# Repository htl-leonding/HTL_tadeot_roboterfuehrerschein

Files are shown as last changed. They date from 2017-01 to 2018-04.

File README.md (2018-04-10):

# Roboter Führerschein (Tag der offenen Tür)
Dieses Repository umfasst alle wichtigen Infos sowie den Server und den Client für das Projekt **HOTRoad** (_Himbeerkuchen on the Road_) welches am Tag der offenen Tür unter dem Namen **Roboter Führerschein** vorgeführt wird.

# [DropboxLink](https://www.dropbox.com/sh/1ua68h7xghiqnpn/AAAmZcrnHf75XxftolFobO0Ba?dl=0)

### Was ist alles am Repo?
 - **Client**: Hier befindet sich der Source Code beider Clients, mit denen man den Roboter ansteuren kann. Es gibt einen Desktop-Client für  den Rechner und einen Andriod-Client für das Handy. 
 - **Server**: Hier befindet sich der Source Code für den Server (denn man auf dem Raspberry ausführen muss) welcher die Signale der Clients interpretiert.
 - **FührerscheinBuilder**: Hier befindet sich die Anwendung, mit der man die Führerscheine erstellen und als PDF exportieren kann um diese anschließend auszudrucken.
 - **Requirements**: Hier befindet sich einerseits die mpjpg_streamer Library welche für den Raspberry zum Streamen der Kamerabilder benötigt wird, und die JoyToKey Anwendung welche man benötigt um die Controller Inputs auf die richtigen Tastatur Inputs umwandelt.
 - **Documents**: Hier befinden sich alle wichtigen Information für das Projekt sowie Schaltplan, Liste der Teile etc... .

### Installation Guide
**WARNING**: This guide assumes you have a Raspberry Pi (Model B or newer/better) with Raspbian OS installed and 2 free USB ports. The Raspberry Pi must be connected to the internet and you’ll need to SSH onto it. You should also know how to gain superuser rights, because they are a necessity throughout the guide.

1. **Assembly of the car**<br>
    Use the parts from the given list (_“Stückliste.ods”_) and assemble them as followed:<br>
    ## Circuit Diagram:    
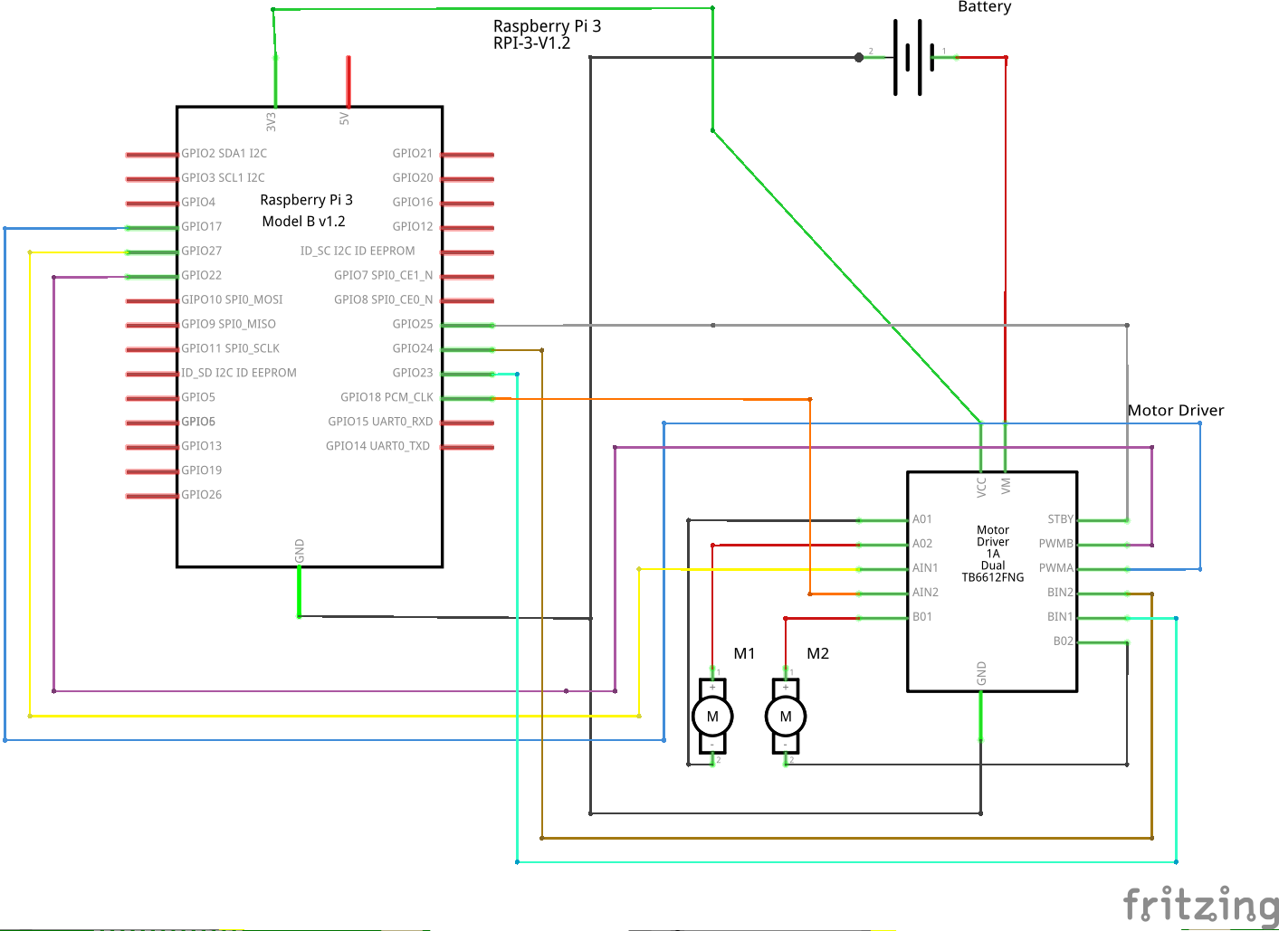
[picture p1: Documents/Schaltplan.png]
Schaltplan
     <br>
    
    ## Fritzing:
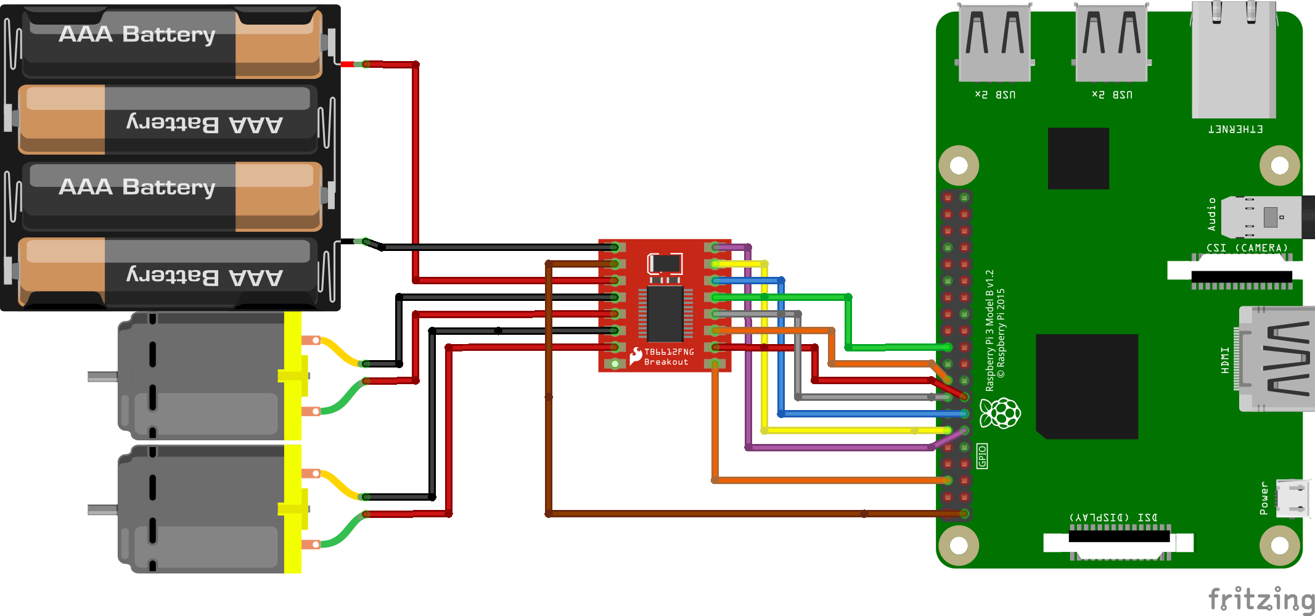
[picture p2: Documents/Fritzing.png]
Fritzing
    
    
2. **Packages, packages, packages**<br>
    You now need to install a few packages, which are necessary for **HOTRoad** to even function. You’ll need:   
    
    ```
    $ apt-get install hostapd isc-dhcp-server libjpeg8-dev imagemagick libv4l-dev
    ```
    Now comes the fun part.

3. **Configuring hostapd**<br>
    Open up “/etc/hostapd/hostapd.conf” add the following lines:
    ```
    interface=wlan0
    driver=nl80211  ---> Use rtl871xdrv for EDIMAX adapters
    ssid=HOTRoad
    hw_mode=g
    channel=11
    wpa=1 wpa_passphrase=himbeerkuchen
    wpa_key_mgmt=WPA-PSK
    wpa_pairwise=TKIP CCMP
    wpa_ptk_rekey=600
    macaddr_acl=0
    ```

    If you know how, change the settings appealing to your needs!
    Now open up **“/etc/default/hostapd”** and add:
	```
	DAEMON_CONF=”/etc/hostapd/hostapd.conf”
    ```
    
    **For EDIMAX adapters**<br>
    If you are using a EDIMAX adapter you need to change the hostapd binary. Copy the given hostapd binary with the following script:
	```
	 $ mv /usr/sbin/hostapd /usr/sbin/hostapd.bak
	 $ cp /home/pi/dat/hostapd /usr/sbin/
	```
	
4. **Configuring isc-dhcp-server**<br>
    Edit **“/etc/dhcp/dhcpd.conf”** and add the following:
	```
	subnet 10.10.0.0 netmask 255.255.0.0 {
        range 10.10.0.25 10.10.0.50;
        option domain-name-servers 8.8.4.4;
        option routers 10.10.0.1;
        interface wlan0;
    }
    ```

    Override the existing settings in **“/etc/network/interfaces”** with:
	```
	iface wlan0 inet static
	address 10.10.0.1
	netmask 255.255.255.0
	```

5. **Configuring mjpg-streamer**<br>
    You need to build the given version of mjpg-streamer (no really, only the given version is working – at least for me). To achieve this you need to follow these commands:
    ```
    $ cd /home/pi/mjpg-streamer
	$ ln –s /usr/include/linux/videodev2.h
    $ make mjpg_streamer input_file.so output_file.so
    ```

6. **Start scripts**<br>
    Everything is going well? This is the last step in this guide. You now need to tell the system to start everything when it boots. Create a file called **"hrinit.sh"** and add the following lines:
    ```
    #!/bin/sh
    sleep 15
    cd "/home/pi/mjpg-streamer/"
    sudo java -jar "home/pi/dist/HOTRoad.jar" & sudo mjpg_streamer -i "./input_uvc.so -n -y -f 15 -q 20 -r 320x240" -o "./output_http.so -n -w ./www -p 80"
    ```
    Save the file under **“/etc/init.d/”** and run:
	```
	$ update-rc.d /etc/init.d/hrinit.sh defaults
    ```
    Ignore the warnings: You are running a patchwork product.
    Now run these:
	```
	$ update-rc.d hostapd enable
	$ update-rc.d isc-dhcp-server enable
    ```
### Good Job. You are done. Now restart your Raspberry Pi and get driving.

PS.: Addition from 2016
In the new pimped version you need to create a folder “/home/pi/music”. You also need to build the JARs yourself. The hostapd binary and the mjpg-streamer source code are under the folder “Other”.

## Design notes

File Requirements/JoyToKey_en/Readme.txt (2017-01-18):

======================================================================

                        JoyToKey Version 5.8.2

                      Copyright(C) 1999-2015, JTK

======================================================================

1. OVERVIEW
-----------
This software enables you to control various windows applications (e.g.
a web browser, games on the web, Photoshop shortcuts, Microsoft office,
and even Windows itself) by using your favorite joystick.  Whenever you
press joystick buttons and sticks, JoyToKey will convert the input into
keyboard strokes and mouse movements so that the target application works
as you pre-configured!

NOTE: On Windows Vista, 7, 8 or 10, you may not be able to control some
applications due to enhanced security control.  If you encounter such
problems, try to launch JoyToKey.exe by opening right-click popup menu
and selecting "Run As Administrator".

2. KEY FEATURES
---------------
* Create multiple configuration files
  You can create multiple configuration files and switch them at any time.
  For example, create one config for a game, and create another one for
  web browsing.  JoyToKey also supports the automatic switching of an
  active configuration file when the target application changes.

* Assign multiple keys for each button
  For example, you can assign a combination of Alt+F4 for one joystick
  button.

* Mouse emulation
  You can also emulate mouse cursor movements, clicks and wheel rotation.

* Automatic repeat of button input or toggle input

* Virtual joystick setting
  Even if you have only one joystick, you can configure button mapping for
  multiple virtual joysticks (e.g. one joystick for default key mapping,
  another virtual joystick for registering function keys or shortcuts, and
  yet another virtual joystick for mouse control).
  You can switch to those virtual joystick mappings temporarily by pressing
  special buttons.

3. HOW TO INSTALL
-----------------
Simply unzip the archive file into some folder.
To uninstall this software, you only need to remove that folder.
(This software doesn't use a registry)

Please make sure that the installed folder is not write 
protected as it needs to save configuration files in the same folder.

System requirement:
  * OS: Windows 10, 8.1, 8, 7, Vista, XP
  * DirectX 7.0 or above

4. USAGE
--------
* Press "Create" button and create a new configuration file

* In the right panel, choose a button from the list and double click 
(or press enter key) to open a button assignment window.

* For example, if you want to control Internet Explorer with joysticks,
  you could configure as follows:
    "Back" : Alt + Left
    "Close Window" : Alt + F + C
    "Move To Menu" : Alt + F
  And you may also want to add mouse cursor movement, wheel etc.

* If you are a new user and you have some trouble configuring JoyToKey,
  please follow the instructions below.

  i) I recommend you to try to use it with a simple application like
     "Notepad.exe".

  ii) Please configure a few joystick buttons mapping to "a", "b" keys.
     And then open a Notepad and press those joystick buttons.
     Character "a" and "b" should be entered in the Notepad.
     (Be sure to keep the JoyToKey program running, iconized in the task
      tray at the bottom of the desktop.)

  iii) If it doesn't work, go to menu "Configuration -> Calibrate joystick
     property" (or go to "control panel" from Windows Start menu), and
     check game controller properties.  Please make sure your joystick
     is recognized and sticks and buttons are calibrated properly.

5. TIPS
-------
* SHIFT key function (switch to other joystick mapping temporarily)
  At first, this feature (aka virtual joystick) may sound difficult to
  understand, but it is very useful as it enables you to configure many
  key mapping, more than the number of buttons you actually have!

  For example, you may have only one joystick with only 6 buttons.
  Then, you can only assign 6 different key mapping by default.  However,
  by assigning one button to switch to a virtual joystick-2, you can assign
  5+5=10 different key mappings (Note: 1 button is used to switch between
  two mappings).  You could further assign another button to switch to a
  virtual joystick-3, which will result in total 5+4+4=13 different key
  mappings.

  Normally, you define the most frequently used key mappings for a physical
  joystick-1.  Then, you could define less used key mappings for virtual
  joystick-2, 3, 4, ...

* Configuration file (*.cfg) is simply a text file. So, If you want to
  rename the configuration, copy the configuration, backup the files etc.,
  terminate JoyToKey and simply rename or copy the file (*.cfg) in Explorer.

6. ABOUT JOYTOKEY
-----------------

Firstly, thank you very much for downloading and using JoyToKey.

JoyToKey is a shareware, but you can freely try it until you like it without
much limitation in functionality.  After trial, if you find it useful, you
can purchase a license key from the website.

http://joytokey.net/en/purchase

(or simply go to JoyToKey menu "Help" -> "Purchase License Key")

The price is $7.00, and it can be paid through share*it! or PayPal.

You can install and use JoyToKey on multiple PCs for your personal use.

Your contribution is greatly appreciated and will be used to continue the
development of JoyToKey.

DISCLAIMER:
This product comes with no warranty. Use it at your own risk. The author
takes no responsibilities of any sort related to the use of this product.

JoyToKey is by no means perfect and may not work for certain type of 
applications.

If you have some comments, suggestions or bug reports, please feel free 
to send an email to the author.  Due to the number of emails, you may not
receive a response, but I will try my best to read all the messages and
reflect them in the future release.

Thanks again for using JoyToKey, and I hope it'll help you to improve
your PC life.

Best Regards,

JTK

Homepage: http://joytokey.net/
E-Mail: JoyToKey@jtksoft.net

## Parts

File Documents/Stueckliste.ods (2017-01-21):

Marke | Type | Link | Preis | Info
SparkFun Electronics | TB6612FNG Motor -Treiber | Motor Treiber (http://www.physicalcomputing.at/shop/article_A-1123300k/DC-Motor-Treiber-1A%2C-Dual.html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) | 6,90 EUR + 5,50 EUR Versand
Raspberry Pi Foundation | Raspberry Pi B-Modell | RaspberryPi (https://geizhals.at/eu/raspberry-pi-modell-b-rev-2-0-a874581.html) | Etwa 25 EUR + Versand
Conrad | 9V Alkaline Batterie | Batterie (http://www.conrad.at/ce/de/product/658014/9-V-Block-Batterie-Alkali-Mangan-Conrad-energy-6LR61-9-V-1-St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) | 3,49 EUR
Conrad | SZ-PP2011L Akku-Pack |  | 19,99 EUR | Alternativ: Beliebiger Akku mit 5V Ausgangsspannung und mind. 400mA Ausgangsstrom
Netgear | WNA1100 Wireless USB Adapter | WLAN-Stick (http://www.amazon.de/Netgear-WNA1100-100PES-USB-Adapter-mit-Cradle/dp/B00380DI9Y) | 13,95 EUR
Microsoft | Xbox 360 - Live Vision Kamera | Kamera | 15,99 EUR | Alternativ: Beliebige Kamera mit YUV Funktion
SanDisk | SD-Card Ultra 8GB | SD-Card (http://www.amazon.de/SanDisk-Ultra-Class-Speicherkarte-UHS-I/dp/B00812K4V4?s=aps) | 14,65 EUR

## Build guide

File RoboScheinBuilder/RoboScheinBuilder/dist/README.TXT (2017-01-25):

========================
BUILD OUTPUT DESCRIPTION
========================

When you build an Java application project that has a main class, the IDE
automatically copies all of the JAR
files on the projects classpath to your projects dist/lib folder. The IDE
also adds each of the JAR files to the Class-Path element in the application
JAR files manifest file (MANIFEST.MF).

To run the project from the command line, go to the dist folder and
type the following:

java -jar "RoboScheinBuilder.jar" 

To distribute this project, zip up the dist folder (including the lib folder)
and distribute the ZIP file.

Notes:

* If two JAR files on the project classpath have the same name, only the first
JAR file is copied to the lib folder.
* Only JAR files are copied to the lib folder.
If the classpath contains other types of files or folders, these files (folders)
are not copied.
* If a library on the projects classpath also has a Class-Path element
specified in the manifest,the content of the Class-Path element has to be on
the projects runtime path.
* To set a main class in a standard Java project, right-click the project node
in the Projects window and choose Properties. Then click Run and enter the
class name in the Main Class field. Alternatively, you can manually type the
class name in the manifest Main-Class element.

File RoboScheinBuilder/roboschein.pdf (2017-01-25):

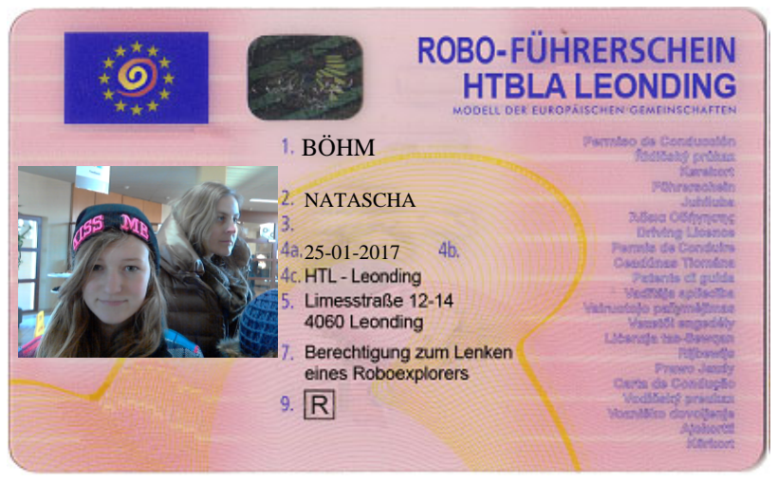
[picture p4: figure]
BÖHM; NATASCHA

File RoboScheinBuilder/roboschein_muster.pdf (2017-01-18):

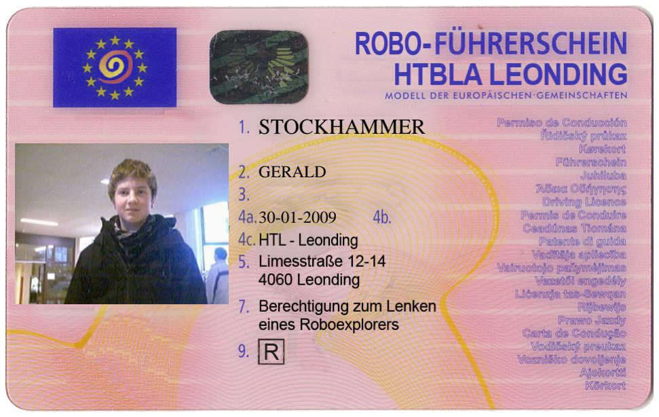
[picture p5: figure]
STOCKHAMMER; GERALD

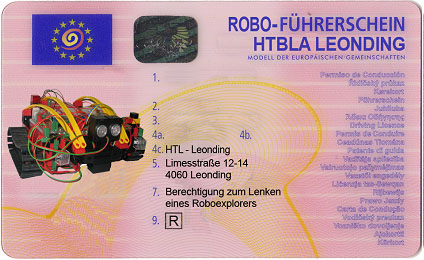
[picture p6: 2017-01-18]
RoboScheinBuilder/robo-schein.jpg

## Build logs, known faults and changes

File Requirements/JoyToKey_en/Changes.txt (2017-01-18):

---------------------------
  JoyToKey change history
---------------------------

Ver 5.8.2
* Increased the maximum number of joysticks from 16 to 32.

Ver 5.8.1
* Bug fix

Ver 5.8
* Enhanced the support for XBox360 controller.  For example,
  - The silver guide button can be assigned as button 13
  - Left/Right trigger can be assigned as analog input button 11, 12

* Added support for XInput devices besides DirectInput devices.

* Enhanced auto-repeat definition to support more flexible definition.
  (for example, 1.2 times per second, or repeat every 2.5 second)

* Added an ability to show an image file when an active profile is changed.
  Image file can be registered in Options tab for each profile.

* A few minor bug fixes

Ver 5.7.1
* Support "Numpad Enter" key assignment via right-click menu.

* Support up to 4 POV inputs.

* Enhanced the right-click menu on the joystick tab and on the button list
  such that the selected configuration can be copied-to or pasted-from
  a clipboard.

* Enhanced device configuration to support axis mapping for all 8 axes.

Ver 5.7
* Support for an absolute mouse movement (a.k.a. spring mode)
  Mouse cursor can be positioned at a configured center location and can
  be moved within a specified range with an analog input stick. This can
  be useful for an application like a flight simulator easier.

  A regular button can be also used like a mouse shortcut by jumping the
  mouse cursor to a preconfigured position, followed by a mouse click.

* Exposed hidden parameter "AnalogDeadZone" (which is used for DirectInput
  setup) in "Settings -> Configure Joysticks". If you want to minimize the
  input threshold for your device, please try setting it to zero. If you
  need a different threshold for Stick1 and Stick2, you can continue to do
  so in "Options" tab for each profile.

* Enhanced SHIFT key (virtual joystick) function to support delayed switch.
  Combined with a "Button Number Mapping" feature, for example, one button
  can be assigned for both a regular key input (for a short press) as well
  as for a SHIFT function (for a long press).

* Enhanced "Switch depending on how long the button is pressed" in Keyboard2.
  In case the event emulation is not recognized reliably when you press
  the button too quickly, JoyToKey can now hold it for a minimum duration.
  (default 20 msec)

* Other minor bug fixes

Ver 5.6
* Enhanced "Keyboard 2" functionality to support the followings
  - support 4 keys per definition
  - support the rotation of 4 input definitions
  - support auto repeat and toggle configuration

* Upgraded DirectX library version from 7 to 8.

Ver 5.5.x
* bug fixes

Ver 5.5
* Support "Button Alias (Number Mapping)"

  Example Usage1:
    Swap button numbers if the connected joystick has a different button
    layout from your favorite one.

  Example Usage2:
    Associate Button21 with Button1 so that both functions are triggered
    when Button1 is pressed.

  Example Usage3:
    It is also possible to configure some button (e.g. Button22) to be
    triggered when both Button5 and Button6 are pressed simultaneously.

* If some buttons are pressed when profile is changed or SHIFT function
  is triggered, those button press are likely to trigger both old and new
  assignments right before/after the switch.

  It is now possible to define certain duration (e.g. 100 msec) to ignore
  those inputs right after the switch (from preference menu)

* When both mouse cursor movement and mouse click are assigned to a button,
  click&hold will be processed before cursor movement.

* Improved the reliability after resuming from PC sleep.

* Preferences were moved from menu items to a separate window.

* Added an ability to specify the number of buttons to configure.
  (by default 16 buttons, MAX 32 buttons)

* Changed the user interface font to Calibri

* Configuration files are now saved in Unicode format (UTF8+BOM).
  This may fix garbled character issues for the use of non-default
  language.

Ver 5.4.2
* Fixed garbled characters for some non-Japanese PC and keyboard.

* (only for advanced users)
  Support specifying "JoyToKey.ini" file path via registry.
  If you have any reason why you need to forcibly specify "JoyToKey.ini"
  file path (e.g. you're using some launcher like Hyperlaunch), you can
  do so via registry editor.
  1. Run "regedit" program
  2. Create a key "HKEY_CURRENT_USER\Software\JoyToKey"
  3. Create a string value "IniFilePath=c:\whateverpath\JoyToKey.ini"

Ver 5.4.1
* Support various file formats (such as mp3) for sound notifications.

Ver 5.4
* Added an ability to play sound or show tasktray balloon when the
  selected profile is changed.

  - Tasktray balloon can be enabled from "Preferences" menu.

  - Sound notification can be configured for each profile in "Options"
    tab. (currently, only WAV files are supported)

  For example, sound notification could be useful for visually impaired
  users, while they step through different profiles to help them to pick
  the right one.

* The size of profile files is made smaller by eliminating empty lines.

* In case "JoyToKey.ini" file or its directory is not write-able,
  JoyToKey will try to make them write-able.

Ver 5.3.1
* Homepage URL was changed to http://joytokey.net/

Ver 5.3.0
* Support delayed input for a special function to switch profiles.
  If you want to keep JoyToKey running while you're playing a game
  which has a native joystick support, the followings may be useful.
  - Temporarily switch to a profile, which is basically empty
  - But it has one button assigned for switching back to the
    original profile after being pressed for X seconds.

* Control the behaviour when JoyToKey window is active from menu
  "Preferences" ->
    "Don't emulate keyboard input when JoyToKey window is active"
  (by default true)

Ver 5.2.3
* Support emulation for 4th and 5th mouse button.
  They could be useful if you're using mouse gestures with joysticks.

* Turbo mode was enhanced to support up to x16 processing speed.
  However, this is experimental and should not be used for regular use
  as it's very CPU intensive and is likely to slow down the PC.

Ver 5.2.2
* Support for loading configuration files from a common AppData folder
  when it exists. (e.g. C:\ProgramData\JoyToKey)

* Added a new menu "Open file folder in Explorer"

Ver 5.2.1
* Bug fix: garbled characters for allow keys

Ver 5.2.0
* Support the combination of keyboard and mouse click
  Ex) SHIFT+Click, CTRL+Click

  In order to specify a mouse click in keyboard assignment window,
  please right-click the entry box.

* Bug fix: minor bug fix for 5.1.2

Ver 5.1.2
* Bug fix: SHIFT + arrow keys were not properly processed.

Ver 5.1.1
* Mouse cursor emulation with analog sticks is further improved.

Ver 5.1.0
* Mouse cursor emulation is now much smoother with analog sticks,
  by using a continuous acceleration without a threshold.

* In case analog stick input has been wrong, axis mapping can be
  manually specified.
  (Menu: "Preferences" -> "Configure joysticks")

* In case you have multiple joysticks and want to always use one
  of them as "Joystick 2" (or any other joystick number), you can
  define a priority/preferred number for each device.
  (Menu: "Preferences" -> "Configure joysticks")

* Miscellaneous bug fixes.

Ver 5.0.3
* (Improvement) Re-detect joysticks after resuming from sleep.

Ver 5.0.2
* Bug fix: Preference "Highlight buttons when JoyToKey is active" was not
  properly saved.

Ver 5.0.1
* Added a menu "Help -> Overview"
* Added a button "Edit button assignment"
* Minor bug fixes

Ver 5.0
* Support for different key assignments based on analog stick input level.

* Support for different key assignments based on button hold duration.

* Support for rotating key assignments.  For example, whenever the same
  button is pressed, its key assignment can rotate like 
  "A -> B -> A -> B -> A ..."

* Enhanced auto-repeat key functionality.
  The following auto-repeat definitions are newly possible:
  - "1.5 repeats per second"
  - "one repeat per 123.4 seconds"
  - "auto-repeat only after 500 milli-seconds"

* When the main window of JoyToKey is activated and joystick buttons are
  pressed, those buttons will be highlighted in the main window so that
  you can easily see which button corresponds to which row in the config.
  (You can change it back to the old behaviour from menu setting)

* When the window is minimized, icon will be kept in the taskbar by default.
  If you prefer the old behavoir and want to hide it from taskbar, you can
  change it back to the old behavior from settings menu.

* Added a comment field for each button definition.
  For example, you can record a memo like "This button is used for Jump".

* Support for copying joystick configration from one to another.
  Right-click "Joystick 1" header in the main menu, to open a popup menu.

* Support for at maximum 4 key assignments for each button.

* Various small bug fixes

Ver 4.6
* You can choose the default behavior when the target application switches 
  to non-associated appliation.

* When you temporarily switch to the virtual joystick configuration while 
  some button is being pressed, the pressed state will be kept without 
  release event if its original key config and the new key config are the
  same.  (e.g. if the arrow key is assigned for both the original joystick1 
  config and the virtual joystick3 config, then switching between joystick1 
  and joystick3 won't trigger unnecessary release event)

From ver 3.x to ver4.5.x
* It became a shareware soft

* Support for associating config files with applications
  It can automatically switch active configuration file based on running 
applications.

* Support dynamic acceleration of mouse cursor movement
  If you use mouse cursor emulation with analog stick, the speed 
sensitivity can be accelerated at certain threshold.

* Support 4-way and 8-way assignment for POV control

* Auto repeat functionality, ranging from very slow repeat (1 time per 
15 minutes) up to 60 times per second (with 2x processing mode)

* Support for toggle button
  e.g. use it for drag&drop with mouse emulation, or for truly automated 
repeat of keys even when you are away from PC.

* Window size became re-sizable

* Open / Close main window by left-clicking task tray icon 
  (right-click to open popup menu)

* JoyToKey can be started even when joystick is not connected
  And it will automatically detect the newly connected joystick.
  (NOTE: it only works the first joystick.  If you connect the second one
   or more, please press "detect" button manually from preferences panel)

* Several additions in the menu such as
  - copy configuration file
  - open game controller setting from control panel
  - suspend / resume temporalily
  - 2x processing mode (if you want to minimize the input latency, sacrificing extra CPU load)
  - generate debug log

Ver3.x highlights
* Under Windows 2000 or later (including XP), JoyToKey now supports
  some applications using DirectInput.

* Choosing L-Shift, R-Shift, L-Ctrl, ... from the list, you can make
  a distinction between left and right keys.
  (Be careful to select L-Shift or R-Shift or (normal) Shift!
   You have to choose the correct one for the application!)

* Support for POV switches.

* Support for "Switch to the other configuration file" function.

* The configuration file can be easily selected and switched to
  at task tray menu, without opening and activating JoyToKey window.

* The firstly activated configuration file can now be specified
  by command line option at start up time.

* Analog stick can be configured in detail by modifying JoyToKey.ini
  file directly:

  "AnalogDeadZone"  (ranges 0 to 10000: default 1000)
    The center area where subtle input from analog stick is ignored.

  "AnalogSaturation"  (ranges 0 to 10000: default 10000)
    The surrounding area from which additional inputs are saturated.

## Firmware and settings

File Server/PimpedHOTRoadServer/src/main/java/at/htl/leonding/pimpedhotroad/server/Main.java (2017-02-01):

package at.htl.leonding.pimpedhotroad.server;

import at.htl.leonding.pimpedhotroad.server.rework.*;
import at.htl.leonding.pimpedhotroad.server.rework.VehicleServer;

import java.io.IOException;

/**
 * Yeah, the main class.
 *
 * @author Bernard Marijanovic
 */
public class Main {

    public static void main(String[] args) throws InterruptedException, IOException {
//        VehicleServer cs = new VehicleServer(VehicleServer.DEFAULT_PORT,
//                VehicleServer.DEFAULT_MUSIC_DIR);
//        cs.start();
        boolean printedRunning = false;

        VehicleServer.getInstance().setDaemon(false);
        System.out.println("Starting server");
        VehicleServer.getInstance().start();
        while(true){
            while(VehicleServer.getInstance().isRunning() || VehicleServer.getInstance().isAlive()){
                if(printedRunning == false) {
                    System.out.println("Server running");
                    printedRunning = true;
                }
                Thread.sleep(1000);
            }

            printedRunning = false;
            System.out.println("Server crashed. Restarting");

            VehicleServer.getInstance().start();
        }
    }
}

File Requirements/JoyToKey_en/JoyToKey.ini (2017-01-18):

[License]
Key=
TS=42753,639730544
Version=Version 5.8.2

[DirectInput]
AnalogDeadZone=1000
AnalogSaturation=10000

[LastStatus]
AllowMultipleRunning=0
StartIconified=0
ExitMeansMinimize=1
HideWhenMinimized=0
WindowPositionTop=134
WindowPositionLeft=104
WindowWidth=710
WindowHeight=500
SplitterPosition=248
ListColumnWidthButton=75
ListColumnWidthKeyboard=144
ListColumnWidthAuto=44
ListColumnWidthComment=140
FileName=Controller
HighlightButtons=1
HighlightButtonsForAllTabs=0
SkipForegroundProcessing=1
NotifyBalloon=0
NotifySoundFile=
NotifyProfileImage=0
ProfileImageDuration=2000
ProfileImagePosition=3
IgnoreInputAfterProfileSwitch=0
IgnoreInputAfterShiftSwitch=0
ShowDebugLog=0
AccelerationSharpness=3
TurboMode=0
XInputSupport=2

[DeviceConfig]
Count=2

[DeviceConfig-1]
GUID={BECCAD60-DD91-11E6-8001-444553540000}
Name=PS  Converter
PreferredNumber=-1
AnalogDeadZone=1000
AxisMapping=0:1:3:4:2:5:6:7

[DeviceConfig-2]
GUID={BECCFB80-DD91-11E6-8002-444553540000}
Name=USB Game Controllers
PreferredNumber=-1
AnalogDeadZone=1000
AxisMapping=0:1:2:3:4:5:6:7

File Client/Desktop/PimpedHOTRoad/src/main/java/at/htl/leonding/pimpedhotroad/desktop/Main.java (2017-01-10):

package at.htl.leonding.pimpedhotroad.desktop;

import javafx.application.Application;
import javafx.fxml.FXMLLoader;
import javafx.scene.Parent;
import javafx.scene.Scene;
import javafx.scene.image.Image;
import javafx.stage.Stage;

/**
 * Created by kepplinger on 29.12.16.
 */
public class Main extends Application {

    private static Stage primaryStage = null;

    /**
     * @param args the command line arguments
     */
    public static void main(String[] args) {
        launch(args);
    }

    @Override
    public void start(Stage primaryStage) throws Exception {

        //Prevents bad font rendering in Ubuntu
        System.setProperty("prism.lcdtext", "false");
        System.setProperty("prism.text", "t2k");

        Main.primaryStage = primaryStage;

        Parent root = FXMLLoader.load(getClass().getResource("/fxml/view.fxml"));

        Scene scene = new Scene(root);

        Main.primaryStage.setTitle("Robo Führerschein");
        Main.primaryStage.getIcons().add(new Image(getClass().getResourceAsStream("/images/icon.png")));
        Main.primaryStage.setScene(scene);
        Main.primaryStage.centerOnScreen();
        Main.primaryStage.show();
    }

    /**
     * Returns the primaryStage for the Controller to add listeners.
     * @return
     */
    static Stage getPrimaryStage() {
        return primaryStage;
    }
}

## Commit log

2017-01-10 Client und Server hinzugefügt
2017-01-18 Changes Requirements
    [Controller.cfg, Joystick.cfg, Tanzmatte.cfg]
2017-01-19 Documents added
    [Fritzing.fzz]
2017-01-19 Update README.md
    Added Circuit Diagram and Fritzing
2017-01-21 Added Stueckliste
    [Stueckliste.ods]
2017-01-26 Reworked server to be more error-save Reworked impulse-processing Added logging to a logfile
    [ImpulseProcessor.java, Main.java, VehicleServer.java]
2017-01-26 Made buttons look nicer VehicleClient now tries to reconnect
2022-12-15 update variable names for new motor stepper
2022-12-16 Update dance mat button mappings
    [Tanzmatte.cfg]
